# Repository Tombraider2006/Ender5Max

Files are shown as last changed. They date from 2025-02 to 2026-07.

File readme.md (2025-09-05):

<h3 align="right"><a href="https://www.tinkoff.ru/rm/yakovleva.irina203/51ZSr71845" target="_blank">ваше "спасибо" автору</a></h3>
<h3 align="right"><a href="https://t.me/tombraider2006" target="_blank">телеграм канал автора</a></h3>

<h1>ENDER 5 MAX</h1>

Итак вы получили ваш Ender 5 Max.  чтобы не запутаться в мануалах предлагаю маленькую справку по дорожной карте что вам делать дальше.

[**Светлый путь. Дорожная карта что надо сделать с принтером чтобы дальше не мучаться**](/lightway.md)

**Внимание! Ahtung! Attention! все измениения в прошивках вы проводите на свой страх и риск, помните что  после того как вы влезли в програмное или аппаратное обеспечение вы можете потерять гарантию производителя!**

## О прошивке
[**Прошивка и получение root доступа**](/firmware.md)

[**cписок полезных макросов с пояснениями**](/mans/macros.md)

[**Стоковый конфиг**](/stock/)

## Модификации

[**Управляем ретрактом во время печати**](/mans/retract.md) 

[**Установка SFS 2.0**](/mans/sfs2.md) замена стандартного датчика филамента на датчик движения. Предотвратит потерю печати при пробках и петлях в катушках.

[**Установка прошивки Simple Af на Ender 5 Max**](/mans/simpleaf.md) на примере датчика картографер.  

[**Замена хотенда на хотенд от К2**](/mans/k2_hotend.md)

При прошивке SimpleAF понадобится [картографер](https://aliexpress.ru/item/1005006733253744.html?sku_id=12000038123192420)  

[**Прошивка картографера в среде windows с помощью wsl**](/mans/wsl.md)

## О запчастях.

Если необходимо, можно докупить сразу с принтером камеру Nebula . [тут](https://aliexpress.ru/item/1005006159528565.html) или [тут](https://aliexpress.ru/item/1005006124602385.html)

по вопросам приобретения панелей зашивки, а также пластин покрытия стола можно обращаться [@RuLED74](https://t.me/RuLED74)(производство панелей начнется не раньше начала апреля-мая 2025г)

Могу порекомендовать [**магазин на озон**](https://www.ozon.ru/seller/krealiti-3d-427462/?miniapp=seller_427462) и [**магазин в россии**](https://creality-3d.ru/catalog/Ender-5-Max). Не всегда всё есть в наличии но можно и заказать для себя. поставки точно от креалити, а не подделка. В отличии от многих, ребята знают какая запчасть к чему подойдет и могут проконсультировать если надо и проверят. Обычно немного дороже алиэкспресса но надежнее и быстрее. 

## Разное полезное

[**Группа пользователей принтера в телеграм**](https://t.me/Ender_5_Max_Ru)

[**Мини обзор на принтер ENDER 5 MAX**](/review.md)

[**Учебный курс и помощь в прошивке принтера**](/kurs.md)

## ОчУмелые ручки

[**Зачем нам одноплатник?**](/random/pi.md) различные модули которые не могут встать на родную операционную систему однако можно поставить на сторонний сервер **Spoolman**, **Telegram Bot**, **Klipperscreen** написано для к1 серии но с минимальными изменениями применимо и для нашего принтера

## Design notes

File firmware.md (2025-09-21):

<h3 align="right"><a href="https://www.tinkoff.ru/rm/yakovleva.irina203/51ZSr71845" target="_blank">ваше "спасибо" автору</a></h3>
<h3 align="right"><a href="https://t.me/tombraider2006" target="_blank">телеграм канал автора</a></h3>

<h2>Прошивки</h2>

На данный момент получить  `root` можно с помощью прошивки [1.2.0.21](https://www.crealitycloud.com/downloads/firmware/ender-series/ender-5-max) с паролем `creality_2024`

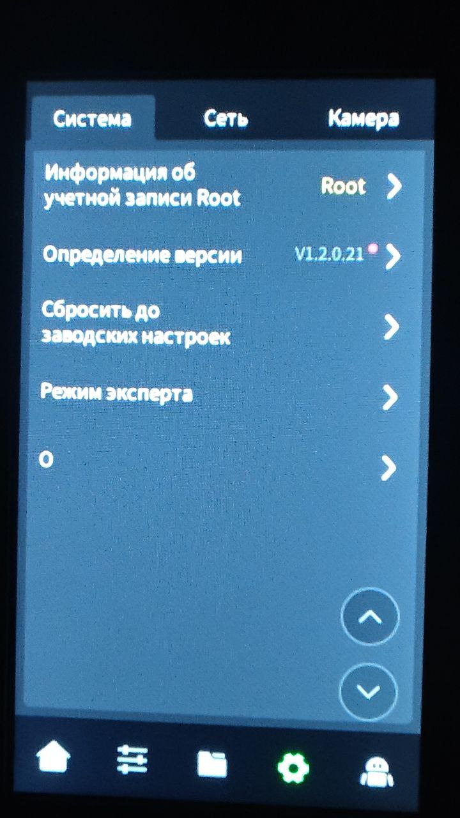
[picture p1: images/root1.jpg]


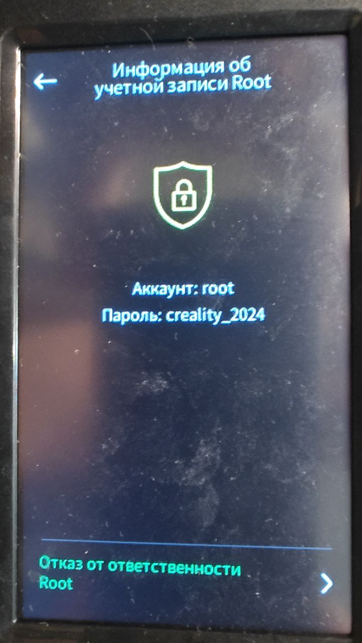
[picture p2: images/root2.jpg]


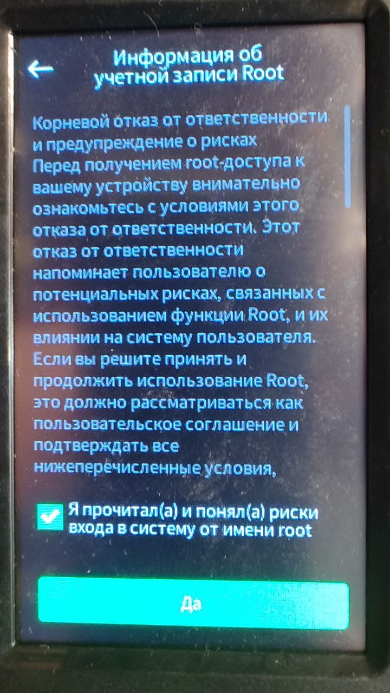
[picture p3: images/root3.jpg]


<details><summary>или с помощью модифицированной прошивки https://github.com/zevaryx/ender-5-max-firmware/releases/latest устарело</summary>

с паролем `creality_2025` 

Если просто залить на флешку установить в принтер и согласиться на обновление не получается и у вас стояла более ранняя прошивка с доступом `root` то можно попробовать заставить обновиться принудительно

```
/etc/ota_bin/local_ota_update.sh /tmp/udisk/sda/*.img
```

или

```
/etc/ota_bin/local_ota_update.sh /tmp/udisk/sda1/*.img
```
после обновления необходимо выключить\включить питание! обязательно!

## Вернуться к прошивке предыдущей 

Чтобы сбросить прошивку, установить более ранюю или вернутся на стоковую прошивку

по ssh заходим и вставляем следующие команды:

```
# Получить текущую версию, независимо от того, какая она
VERSION=$(grep 'ota_version' '/etc/ota_info' | awk -F'=' '{print $2}')

# Принудительно установить версию 1.0.0.0, что ниже минимума
for file in /etc/ota_info /usr/data/creality/userdata/config/system_version.json; do
    sed -i -e "s/${VERSION}/1.0.0.0/g" $file
done

# Перезагрузить систему для принудительной перезагрузки файлов с диска
reboot
```
После этого можно подсунуть системе любую прошивку, она воспримет ее как новую.
</details>
## Установка HELPER-SCRIPT

### Внимание! если вы установите хелпер скрипт то отключите уведомление об обновлении. так же не обновляйте потом прошивку по wifi пока не сбросите принтер до заводских настроек. 

*21.05.2025 -Внимание.*

*Guilois, автор helper script, наконец то обратил внимание на данный принтер и выделил, наконец, ветку под него, но дальнейшего развития не получил, поэтому ставить надо только те пункты которые подойдут нашему принтеру, слепо ставить все подряд нельзя, иначе принтер уйдет в ошибку или перестанет нормально функционировать. 

Пока не приехал ваш картографер, а печатать уже хочется можно облегчить себе жизнь установкой привычной оболочки klipper. Для этого необходимо установить [**хелпер скрипт**](https://guilouz.github.io/Creality-Helper-Script-Wiki/helper-script/helper-script-installation/) и получить базовую функциональность клиппера.

для этого через ssh нам необходимо ввести следующие команды:

```
git clone --depth 1 https://github.com/Guilouz/Creality-Helper-Script.git /usr/data/helper-script
```
после того как скрипт скачается запускаем его

```
sh /usr/data/helper-script/helper.sh
```

пункт 1 install

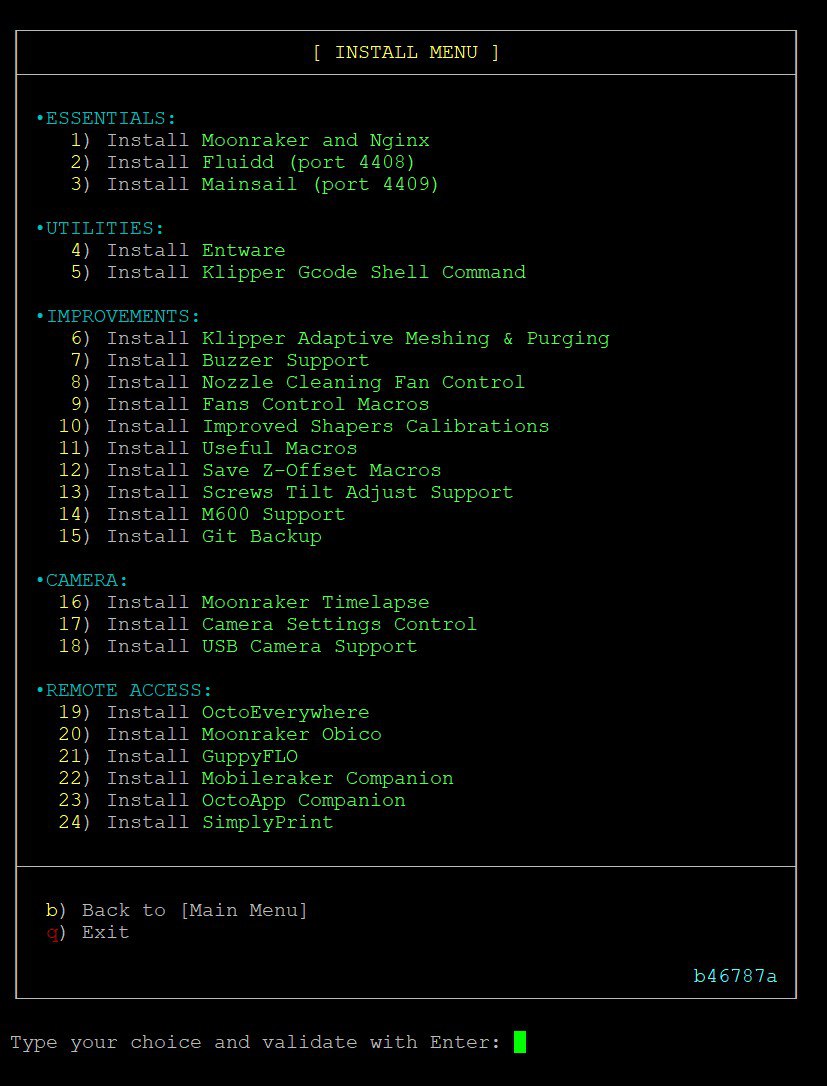
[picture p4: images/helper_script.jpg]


рекомендуемые пункты меню 1, 2, 4, 5, 10. если у вас есть видеокамера то 16.

Лучше сверяйтесь в [**Группе пользователей принтера в телеграм**](https://t.me/Ender_5_Max_Ru) по правильности пунктов. бывает  что могут смениться без предупреждения.

через  браузер теперь мы можем зайти на наш принтер в расширенную вебпанель с доступом к файлам конфигурации и расширенным настройкам. Не забываем указать порт `http://Ваш_ip:4408` если вы установили Fluid и `http://Ваш_ip:4409`  если Mainsail

## После установки

## NEW 
### вариант автоматического внесения изменений

1. Переходим в папку с конфигами принтера. Скачиваем и запускаем скрипт fix_ender5.sh с GitHub

```
wget -q --no-check-certificate https://raw.githubusercontent.com/Tombraider2006/Ender5Max/refs/heads/main/files/fix_e5m.sh -O /tmp/fix_e5m.sh && sh /tmp/fix_e5m.sh
```

<details><summary>Устарело. есть в автоматической версии.</summary>

в вебпанели ищем значок слева {...}  в окошке ищем файл `gcode_macro.cfg` открываем его и мотаем в самый низ

добавим следующий код:

```
[firmware_retraction]
retract_length: 0.45 # безопасное значение для того пластика которым чаще всего печатаете.
retract_speed: 30
unretract_extra_length: 0
unretract_speed: 30

[gcode_shell_command beep]
command: beep
timeout: 2
verbose: False

[gcode_macro BEEP] # звук бип. 
description: Play a sound
gcode:
  RUN_SHELL_COMMAND CMD=beep

[delayed_gcode light_init] 
initial_duration: 5.01
gcode:
  SET_PIN PIN=light_pin VALUE=1

[exclude_object] # исключение обьектов. 

[gcode_macro PID_BED]
gcode:
  PID_CALIBRATE HEATER=heater_bed TARGET={params.BED_TEMP|default(70)}
  SAVE_CONFIG

[gcode_macro PID_HOTEND] # и почему его не было. добавил
description: Start Hotend PID
gcode:
  G90
  G28
  G1 Z10 F600
  M106 S255 #S255 
  PID_CALIBRATE HEATER=extruder TARGET={params.HOTEND_TEMP|default(250)}
  M107

```

сохраняем. 

теперь задачка посложнее. открываем файл `printer.cfg`

ищем параметр `[output_pin Height_module2]` и меняем его на 

```
[output_pin _Height_module2]
```

ищем раздел:

```diff
[output_pin light_pin]
#pin: nozzle_mcu: PB0 #PA10
pin: PC0
value: 0.0
```
меняем на 

```
[output_pin light_pin] #  освещение камеры принтера. косяк прошивки креалити.
pin: !PC0
pwm: True
cycle_time: 0.010
value: 1.0
```

чтобы принтер не шумел обдувом материнской платы при простое. надо заменить раздел

```
[output_pin MainBoardFan]
pin: !PB1
```

меняем на:

```
[controller_fan MCU_fan] # включаем обдув после включения драйверов
pin: PB1
max_power: 1.0
fan_speed: 1
kick_start_time: 0
stepper: stepper_x

```
</details>

Чтобы подготовить принтер к работе пройдем тесты и запишем их в конфиг, сделать это проще чем кажется. Для этого достаточно скопировать код в консоль вебпанели принтера. тесты будут длится около 10-20 минут, после этого принтер перезагрузится и будет готов к работе.

```
PID_BED
PID_HOTEND
INPUT_SHAPER_CALIBRATION
```

## OrcaSlicer
В слайсере орка начиная с 2.3.0 есть готовый профиль под принтер Ender 5 max 

но можно и там найти пару косяков и исправить.

в стартовом коде добавить:

```
M140 S0
M104 S0
```
вот так

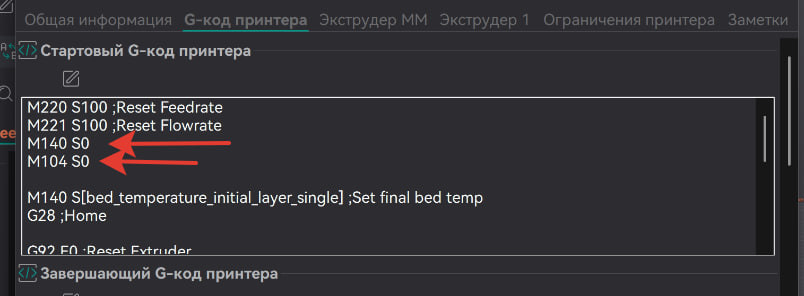
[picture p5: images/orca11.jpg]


**В разделе экструдер** искренно советую понизить скорость ретракта до 30 мм\мсек вместо 50 по умолчанию в 2 местах.

это сохранит шестерни фидера от преждевременного износа.

## Использовать ретракт из прошивки

1. правим стартовый код, добавляем этот блок так:

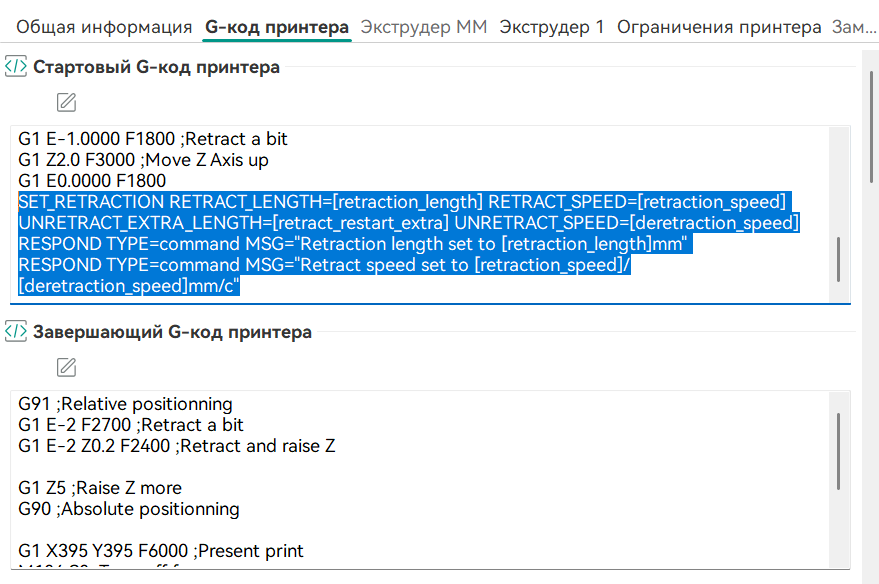
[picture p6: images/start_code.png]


```
SET_RETRACTION RETRACT_LENGTH=[retraction_length] RETRACT_SPEED=[retraction_speed] UNRETRACT_EXTRA_LENGTH=[retract_restart_extra] UNRETRACT_SPEED=[deretraction_speed]
RESPOND TYPE=command MSG="Retraction length set to [retraction_length]mm" 
RESPOND TYPE=command MSG="Retract speed set to [retraction_speed]/[deretraction_speed]mm/c"

```

2. поставим галку тут

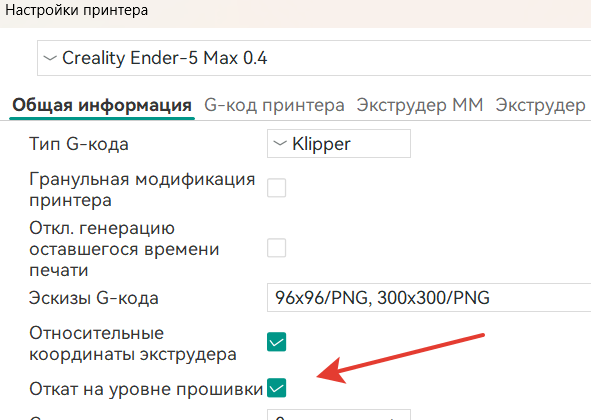
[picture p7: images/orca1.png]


3. потом убираем галку тут

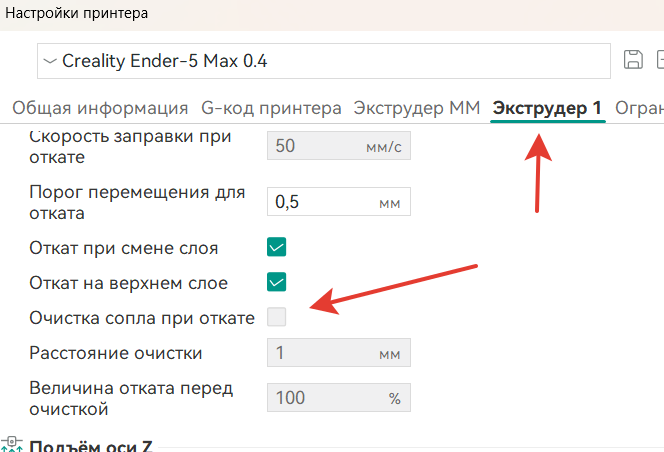
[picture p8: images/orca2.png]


4. не забываем указывать в пластике указывать откат настроенный.

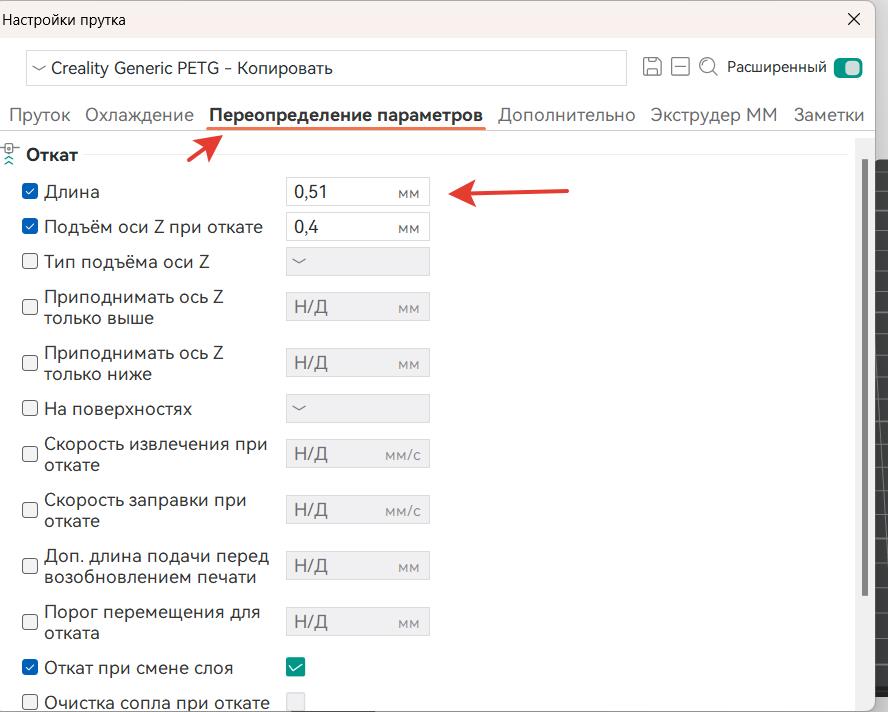
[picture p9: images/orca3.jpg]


## Посмотреть стоковые файлы конфигурации 

1.2.0.10 [тут](/stock/config_1.2.0.10/)

1.2.0.20 [тут](/stock/config_1.2.0.20/)

1.2.0.21 [тут](/stock/config_1.2.0.21/)

На данный момент (август 2025) одна из самых допиленных версий прошивок это от pelkorp с его [**SimpleAF**](https://pellcorp.github.io/creality-wiki/).  К ее недостаткам можно отнести только что поставить можно **!!!только** на картографер и бекон. связано это с тем что не смогли подружить с новым клиппером плату головы а точнее акселерометр. так как в картографере и беконе внутри плат есть акселерометры свои, вышли из положения таким образом.  

Вполне возможно что через некоторое время ситуация измениться.  

Если вы захотите использовать guppyscreen в SimpleAF то необходимо [повернуть экран на 90 градусов.](https://github.com/Tombraider2006/Ender5Max/blob/main/mans/simpleaf.md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) вот [**модель**](/mans/Ender5MaxTiltedScreenMount.stl) чтобы закрепить экран в горизонтальном положении. 

### Если получаем ошибку 2069 (уже есть в автоматическом скрипте)

В файле `printer.cfg` находим разделы и удаляем.

```diff
###喷头前面风扇
[output_pin fan0]
pin: !nozzle_mcu:PB15
pwm: True
cycle_time: 0.01
hardware_pwm: false
value: 0.00
scale: 255
shutdown_value: 0.0
[output_pin en_fan0]
pin: nozzle_mcu: PB6
pwm: False
value: 1.0

###喷头后面风扇
[output_pin fan1]
pin: !nozzle_mcu:PA9
pwm: True
cycle_time: 0.01
hardware_pwm: false
value: 0.00
scale: 255
shutdown_value: 0.0
[output_pin en_fan1]
pin: nozzle_mcu: PB9
pwm: False
value: 1.0

```
заменяем на:

```

[multi_pin part_fans]
pins:!nozzle_mcu:PB15,!nozzle_mcu:PA9

[multi_pin en_part_fans]
pins:nozzle_mcu:PB6,nozzle_mcu:PB9

[fan_generic part]
pin: multi_pin:part_fans
enable_pin: multi_pin:en_part_fans
cycle_time: 0.0100
hardware_pwm: false
```

в файле `gcode_macro.cfg` ищем разделы и удаляем:

```diff
[gcode_macro M106]
gcode:
  {% set fan = 0 %}
  {% set value = 255 %}
  {% if params.S is defined %}
    {% set tmp = params.S|int %}
    {% if tmp <= 255 %}
      {% set value = tmp %}
    {% endif %}
  {% endif %}
  {% if params.P is defined %}
    {% set value = (255 - printer["gcode_macro PRINTER_PARAM"].fan1_min) / 255 * tmp %}
    {% set value = printer["gcode_macro PRINTER_PARAM"].fan1_min + value %}
    {% if value >= 255 %}
      {% set value = 255 %}
    {% endif %}
    SET_PIN PIN=fan1 VALUE={value}

    {% set value = (255 - printer["gcode_macro PRINTER_PARAM"].fan0_min) / 255 * tmp %}
    {% set value = printer["gcode_macro PRINTER_PARAM"].fan0_min + value %}
    {% if value >= 255 %}
      {% set value = 255 %}
    {% endif %}
    SET_PIN PIN=fan0 VALUE={value}
  {% else %}
    {% set value = (255 - printer["gcode_macro PRINTER_PARAM"].fan1_min) / 255 * tmp %}
    {% set value = printer["gcode_macro PRINTER_PARAM"].fan1_min + value %}
    {% if value >= 255 %}
      {% set value = 255 %}
    {% endif %}
    SET_PIN PIN=fan1 VALUE={value}

    {% set value = (255 - printer["gcode_macro PRINTER_PARAM"].fan0_min) / 255 * tmp %}
    {% set value = printer["gcode_macro PRINTER_PARAM"].fan0_min + value %}
    {% if value >= 255 %}
      {% set value = 255 %}
    {% endif %}
    SET_PIN PIN=fan0 VALUE={value}

  {% endif %}
  {% if tmp < 1 %}
    {% set value = tmp %}
    SET_PIN PIN=fan0 VALUE={value}
    SET_PIN PIN=fan1 VALUE={value}
  {% endif %}

[gcode_macro M107]
gcode:
  {% if params.P is defined %}
    SET_PIN PIN=fan0 VALUE=0
    SET_PIN PIN=fan1 VALUE=0
  {% else %}
    SET_PIN PIN=fan0 VALUE=0
    SET_PIN PIN=fan1 VALUE=0
  {% endif %}

```
заменяем на:

```
[gcode_macro M106]
description: Set Fan Speed. P0 for part
gcode:
  {% set fan_id = params.P|default(0)|int %}
  {% if fan_id == 0 %}
    {% set speed_param = params.S|default(255)|int %}
    {% if speed_param > 0 %}
      {% set speed = (speed_param|float / 255) %}
    {% else %}
      {% set speed = 0 %}
    {% endif %}
    SET_FAN_SPEED FAN=part SPEED={speed}
  {% endif %}

[gcode_macro M107]
description: Set Fan Off. P0 for part
gcode:
  SET_FAN_SPEED FAN=part SPEED=0

[gcode_macro TURN_OFF_FANS]
description: Stop chamber, auxiliary and part fan
gcode:
    SET_FAN_SPEED FAN=part SPEED=0

[gcode_macro TURN_ON_FANS]
description: Turn on chamber, auxiliary and part fan
gcode:
    SET_FAN_SPEED FAN=part SPEED=1

```
в самом верху файла ищем  и удаляем строки

```
variable_fan0_min: 90 #240 #90
variable_fan1_min: 70 #240 #70
```

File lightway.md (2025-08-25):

# Светлый путь

1. собираем принтер. проверяем комплектацию. Запускаем принтер проходим начальную калибровку.  если возникают ошибки не переживаем ищем ответы в чате.
2. прошиваем принтер на [**прошивку в которой есть доступ root**](/firmware.md). Без этого принтер практически калека.
3. Заказываем [картографер](/mans/simpleaf.md), [sfs 2.0](/mans/sfs2.md)  на алиэкспресс. Ждем зеленея от надежды. Ищем в мануалах файлы моделей необходимых для установки, не торопясь распечатываем. Возможно не спервого раза. 
4. Пока ждем модели снимаем карту стола.  видим большой горб в 1-2мм на стол, не расстраиваемся идем в чат узнаем что нам надо купить мягкое железо, кусок стекла 415х415мм и еще одно магнитное основание.
5. Регулируем ремни. Мануал будет позже. пока можно посмотреть видео на ютубе от креалити. модели упоров скачать [тут левый](/files/X-axis+tensioning+tool-20250220.stl) [тут правый](/files/Y-axis+tensioning+tool-20250220.stl)
6. Получаем детали, устанавливаем, [датчик движения филамента sfs 2.0](/mans/sfs2.md).
7. Прошиваем картографер [**так**](https://pellcorp.github.io/creality-wiki/cartographer_flashing/#flashing-k1-firmware-via-dfu-mode) или [**так**](/mans/dfu.md)
8. Устанавливаем картографер на принтер. Модели для печати смотрим в пункте 9. Вспоминаем, что забыли купить стяжки чтобы прикрепить провод, плюемся, идем в ближайший магазин покупаем, крепим.
9. Устанавливаем [**прошивку SimpleAF**](/mans/simpleaf.md) 
10. Наши мучения окончены, забываем про софт креалити. Никакие обновления от них в будущем вам не нужны!

## Наши руки не для скуки.

1. Если вам не хватило развлечений, то пишем в [**магазин на озон**](https://www.ozon.ru/seller/krealiti-3d-427462/?miniapp=seller_427462) и [**магазин в россии**](https://creality-3d.ru/catalog/Ender-5-Max) что хотим себе зашивку на принтер. Это даст возможность не только круто выглядеть но и печатать принтеру высокотемпературными пластиками такими как АБС. 
2. Очень предусмотрительно с Вашей стороны будет заказать шестерни экструдера к1с. Да-да, фидер на принтере именно от него. так что смело заказываем. 

3. Сопла для принтера - расходник. Так что заказываем тоже. Ссылка на магазин выше.
4. Возможно вас заинтересует возможность [**смены хотенда на хотенд от К2**](/mans/k2_hotend.md).
5. [**кастомные петли для передней дверцы зашивки**](/files/door190.zip), в отличии от штатных у которых 100 градусов открытие на 190  градусов

BOM
Ось **М3х30**, под нее просто нарезать резьбу, крепление **М3х14**, в **вплавляемые гайки**.

Счастливого светлого пути в мир 3д печати!

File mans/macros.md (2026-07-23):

<h3 align="right"><a href="https://www.tinkoff.ru/rm/yakovleva.irina203/51ZSr71845" target="_blank">ваше "спасибо" автору</a></h3>
<h3 align="right"><a href="https://t.me/tombraider2006" target="_blank">телеграм канал автора</a></h3>
<h5 align="right">поставьте "звездочку" проекту. так другим пользователям легче его найти.</h5>

## cписок полезных макросов с пояснениями

После установки хелпер скрипта открывая вашу панель вы можете увидеть огромную "простыню" с всевозможными макросами. В основном они системные и не предполагают никакого взаимодействия с вами. Они от системы для системы и про систему. Чтобы не путаться и не захламлять интерфейс можно провести несколько простых операций:

1 - открываем настройки

2 - нажимаем макросы

3 - добавить категорию

4 - вписываем название категории (у меня это "тесты")

5 - жмем сохранить

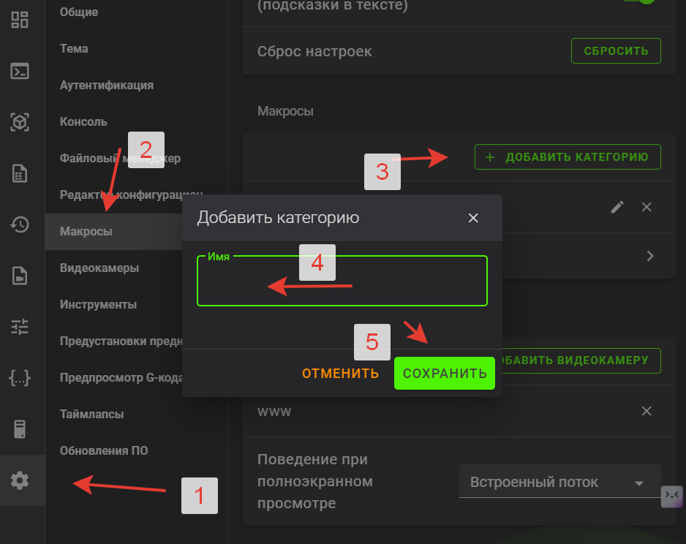
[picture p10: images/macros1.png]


Теперь переходим в раздел "вне категории" и по следующему списку выбираем макрос и нажимаем на него и выбираем ему нашу свежесозданную категорию

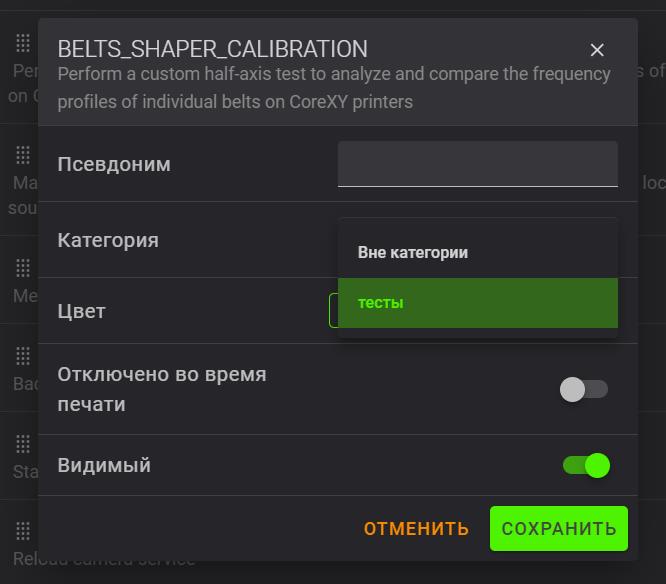
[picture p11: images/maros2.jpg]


`BELTS_SHAPER_CALIBRATION` делает тест резонансов и создает график натяжения ремней

`EXCITATE_AXIS_AT_FREQ` макрос тестирования на определенной частоте резонансов для выявления дефектов сборки

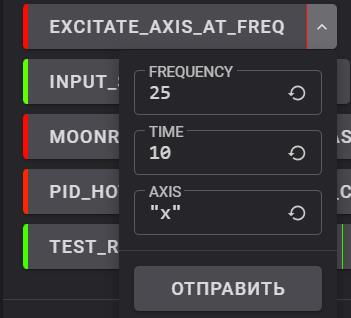
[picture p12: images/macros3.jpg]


На картинке выше мы видим значения по умолчанию. на частоте 25 герц в течении 10 секунд трясем осью икс.  для проведения теста мы ставим 3-5 секунд и перебором частот 25, 27, 30.. и т.д. находим частоту на которой вибрации максимальны. Далее ставим время теста 30-40 секунд и пальпируя корпус находим узел который  вызывает резонанс.  Внешним осмотром выявляем проблему(выкрутился болтик, отклеилась панель, недотянут винт и прочее)  

`INPUT_SHAPER_CALIBRATION` делает тест резонансов и записывает результат в `printer.cfg`

В стоковой прошивке выбор шейперов ограничен `ei` что далеко не оптимально. Helper script решает эту проблему, поэтому после установки скрипта необходимо использовать этот  макрос для установки правильных шейперов.

`TEST_RESONANCES_GRAPHS` делает тест резонансов и записывает его в график.

На основании графика легче понять какие есть проблемы в кинематике, выбрать максимальные ускорения в слайсере, проверить насколько правильно автокалибратор поставил значения в `printer.cfg` 

После окончания теста в папке: `/Helper-Script/improved-shapers` будут находится наши графики. 

В случае прошивки Simple AF графики будут в папке `/images`

`PID_BED` это процедура калибровки, которая гарантирует, что принтер всегда будет поддерживать стабильную заданную температуру . PID (пропорционально-интегральная производная) используется в принтерах для поддержания стабильной температуры стола. По умолчанию тест идет на 70 градусах но рядом со значком есть стрелка вниз раскрываем и устанавливаем там температуру на которой мы в основном работаем.

`PID_HOTEND` это процедура калибровки, которая гарантирует, что принтер всегда будет поддерживать стабильную заданную температуру . PID (пропорционально-интегральная производная) используется в принтерах для поддержания стабильной температуры в хотенде. По умолчанию тест идет на 250 градусах но рядом со значком есть стрелка вниз раскрываем и устанавливаем там температуру на которой мы в основном работаем.

`TILT_TABLE` автоматическая регулировка наклона стола. 

**ТОЛЬКО** для прошивки Simple Af Ender 5 Max

Алгоритм:

1. домой по всем осям
2. быстро вниз на 400 (это не до упора)
3. "обман" высоты, как будто Z не 400, а 370 
4. медленно вниз = долгожданный треск ****
5. ещё раз "обман" (контрольный)
6. ещё медленнее и ещё немного потрещим ***
7. быстро вверх почти домой, но нет...
8. дом Z (стандартно домой Z)

Макрос копируем в любое место в printer.cfg
Сохраняем с перезапуском клипера.
Далее в разделе "макросы" видим новый пункт "tilt_table". 
При желании в настройках макросов можно переименовать эту кнопку в привычный язык "наклон" и задать любой цвет (маркер) кнопки. 
Если кого напрягает скорость стола, можете уменьшить или увеличить значение (F1300). 

```
[gcode_macro tilt_table]
gcode:
    G28
    G0 Z400 F1300
    SET_KINEMATIC_POSITION Z=370 
    {% set driver_config = printer.configfile.settings['tmc2209 stepper_z'] %}
    {% set RUN_CUR = driver_config.run_current|float %}
    {% set HOME_CUR = 0.45 %}
    SET_TMC_CURRENT STEPPER=stepper_z CURRENT={HOME_CUR}
    G0 Z400 F600
    SET_KINEMATIC_POSITION Z=390
    G0 Z400 F300
    SET_TMC_CURRENT STEPPER=stepper_z CURRENT={RUN_CUR}
    G0 Z20 F1300
    G28 Z
```

После этого ваша вебпанель приобретет более аккуратный вид и нужные вам макросы будут более наглядно расположены. 

Для прошивки Simple AF все вышесказанное также справедливо, однако чуть другие названия макросов.

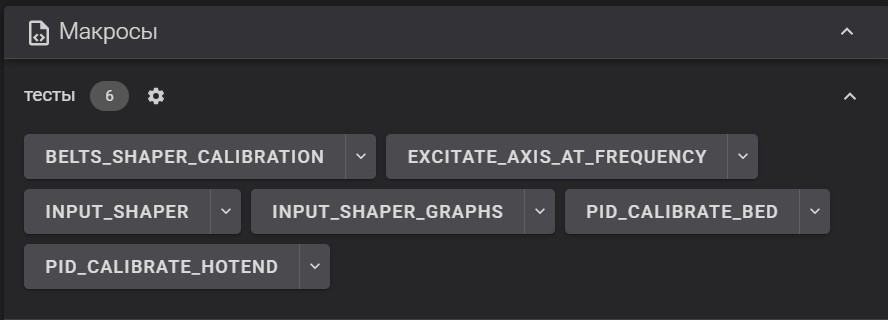
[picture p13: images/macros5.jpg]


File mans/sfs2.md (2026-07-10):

<h3 align="right"><a href="https://www.tinkoff.ru/rm/yakovleva.irina203/51ZSr71845" target="_blank">ваше "спасибо" автору</a></h3>
<h3 align="right"><a href="https://t.me/tombraider2006" target="_blank">телеграм канал автора</a></h3>
<h5 align="right">поставьте "звездочку" проекту. так другим пользователям легче его найти.</h5>

## Установка датчика движения филамента вместо стандартного датчика окончания филамента

[**english version**](/mans/sfs2_en.md)

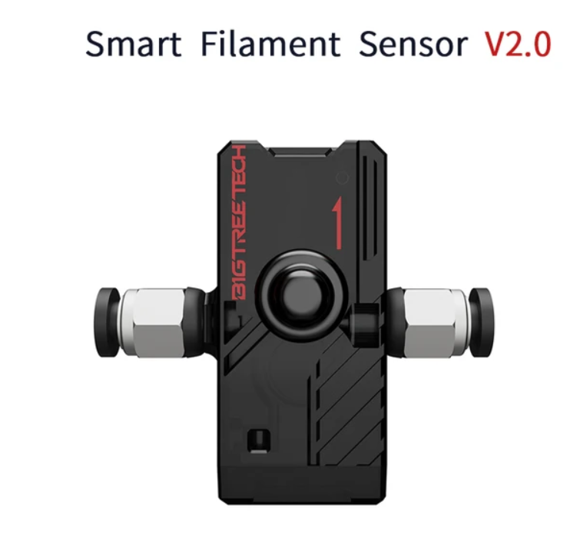
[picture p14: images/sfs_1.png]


Учитывая большую область печати на этом принтере, значительное время печати и высокий расход филамента, контроля только за его окончанием явно недостаточно. Цена ошибки в случае застревания материала будет крайне высока, поэтому установка системы мониторинга не только окончания, но и застревания филамента — отличное решение.

Это позволит минимизировать риски сбоев и избежать потерь времени и материалов.

Так как в обычном датчике филамента у нас три провода, а в sfs 2.0 их 4 то есть два способа установки. 
* первый предполагает соединение только датчика движения вместо окончания филамента, что логично. если нет филамента то он и не движется, что все равно приведет к сработке.
* однако в конструкции нашего принтера не так уж и сложно подвести дополнительный провод, так что этот вариант мы тоже рассмотрим. 

## Первый способ

(замена датчика без дополнительной проводки)

Для этого нам нужно переставить провода в колодку на 4 провода. например так:

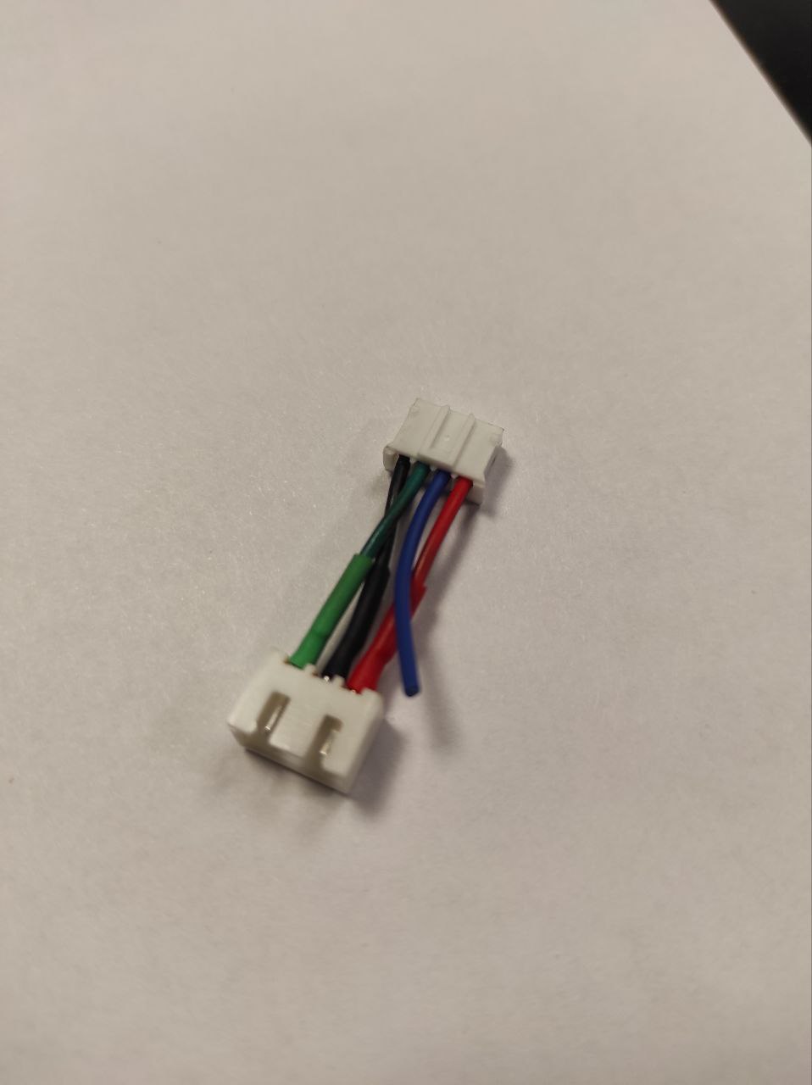
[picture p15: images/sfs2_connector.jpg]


значения на коннекторе следующие:

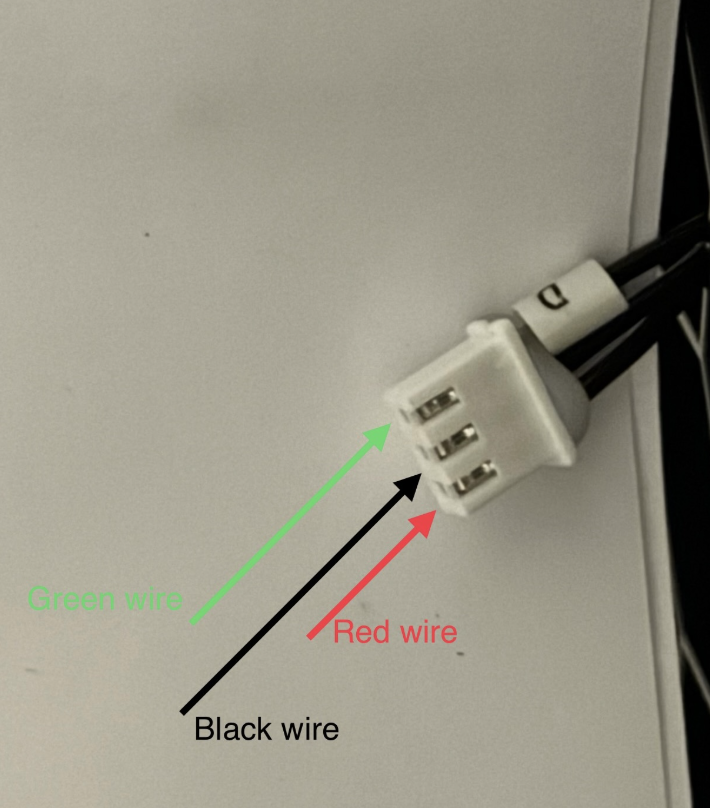
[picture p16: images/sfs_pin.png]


Далее заходим в `printer.cfg` и ищем строки:

```
[filament_switch_sensor filament_sensor] # датчик филамента
switch_pin: !PC6
pause_on_runout: true
```

и заменяем на:

```
[filament_motion_sensor filament_sensor]
detection_length: 5.3
extruder:extruder
pause_on_runout: true
switch_pin: ^PC6
runout_gcode:
  RESPOND TYPE=command MSG="Filament runout/blocked!"
insert_gcode:
  RESPOND TYPE=command MSG="Filament inserted"

```

**или** можем побаловаться с оповещением и при паузе прозвучит несколько звуковых сигналов

```
[gcode_shell_command beep]
command: beep
timeout: 2
verbose: False

[gcode_macro BEEP]
description: Play a sound
gcode:
  RUN_SHELL_COMMAND CMD=beep

[filament_motion_sensor encoder_sensor]
switch_pin: ^!PC6
detection_length: 5.3 # возможно сделать чуть меньше 2.7 по умолчанию
extruder: extruder
runout_gcode:
  _ON_FILAMENT_RUNOUT # для симпл аф!!!!
  RESPOND TYPE=command MSG="Filament runout/blocked!"
  UPDATE_DELAYED_GCODE ID=sfs_alarm DURATION=1
insert_gcode:
  RESPOND TYPE=command MSG="Filament inserted"
  UPDATE_DELAYED_GCODE ID=sfs_alarm DURATION=0

[delayed_gcode sfs_alarm]
# initial_duration: 0
gcode:
  beep
  beep
  beep
  beep
  beep
  beep
  #UPDATE_DELAYED_GCODE ID=sfs_alarm DURATION=1 #если убать комент в начале строки то сигналы будут постоянно.
```
## Второй способ

Если ваши руки не для скуки то можно получить полную функциональность датчика с меньшим количеством отказов для этого надо задействовать все 4 провода от датчика. 

*По сути внутри корпуса sfs находится 2 датчика, датчики наличия филамента, и датчик движения филамента. Для этого нам и нужен четвертый провод.*

Для начала, я соеденил конектор из комплекта через переходник(*дендрофекальным способом*)

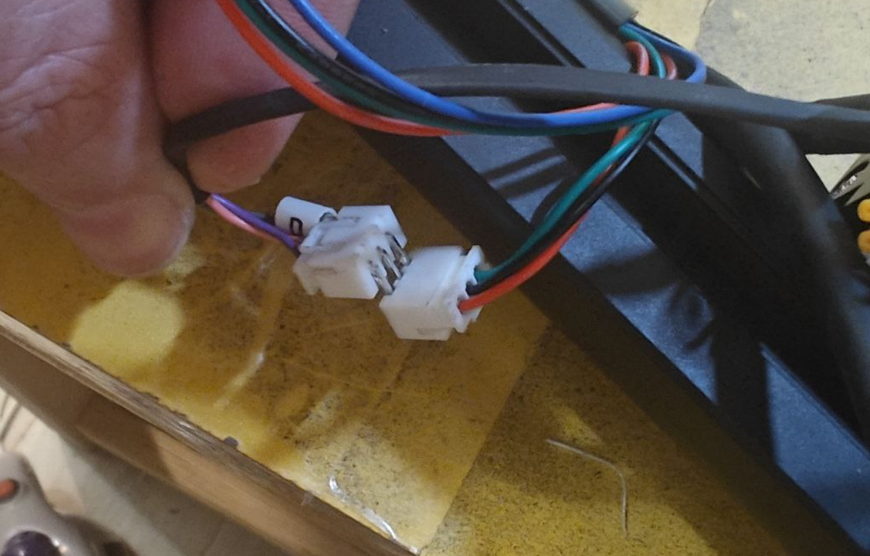
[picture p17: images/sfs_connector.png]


Оставшийся **синий** провод надо протянуть до нашей материнской платы и и припаять к этому выходу. На фото он красный потому что родного провода не хватает буквально 10 сантиметров и я его нарастил. 

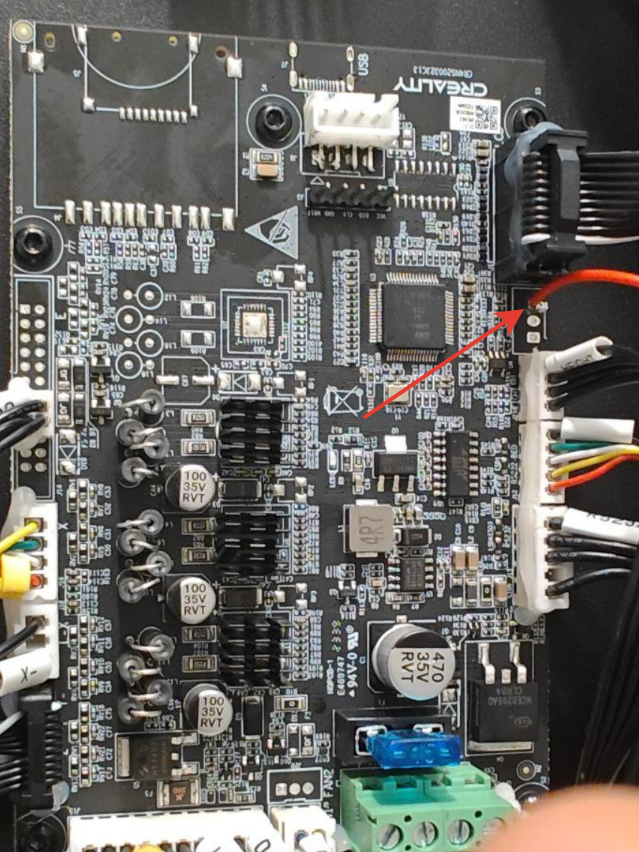
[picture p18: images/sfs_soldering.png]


заходим в `printer.cfg` и ищем строки:

```
[filament_switch_sensor filament_sensor] # датчик филамента
switch_pin: !PC6
pause_on_runout: true
```

и заменяем на:

```
[gcode_shell_command beep]
command: beep
timeout: 2
verbose: False

[gcode_macro BEEP]
description: Play a sound
gcode:
  RUN_SHELL_COMMAND CMD=beep

[filament_switch_sensor filament_sensor]
switch_pin: PA15
pause_on_runout: true
# runout_gcode: PAUSE

[filament_motion_sensor encoder_sensor]
switch_pin: ^!PC6
detection_length: 5.3
extruder: extruder
runout_gcode:
  _ON_FILAMENT_RUNOUT # для симпл аф!!!!
  RESPOND TYPE=command MSG="Filament runout/blocked!"
  UPDATE_DELAYED_GCODE ID=sfs_alarm DURATION=1
insert_gcode:
  RESPOND TYPE=command MSG="Filament inserted"
  UPDATE_DELAYED_GCODE ID=sfs_alarm DURATION=0

[delayed_gcode sfs_alarm]
# initial_duration: 0
gcode:
  beep
  beep
  beep
  beep
  beep
  beep
```
### Установка

Для установки необходимо заменить платформу датчика филамента. модель скачиваем [**отсюда**](/files/Ender5MaxSFSMount.stl) 

Выглядит это так

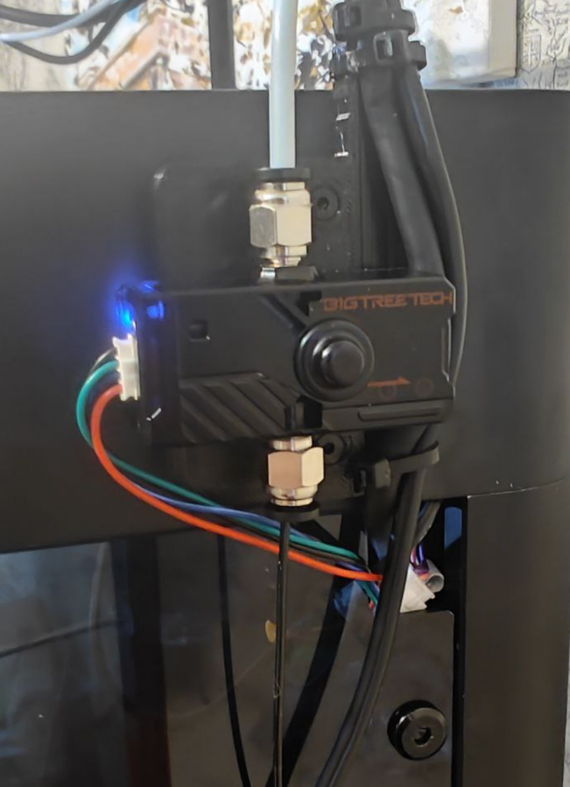
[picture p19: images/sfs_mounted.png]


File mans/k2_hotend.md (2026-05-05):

# Замена хотенда на хотенд от к2

На данный момент с хотендом от Ender 5 Max существует несколько проблем.
1. Нет в продаже самого хотенда. update(уже есть)
2. Нет сопел под него кроме размера 0.4 update(иногда найти тяжело. но уже бывают)
3. Из-за оcобенностей конструкции частые протечки сверху хотенда со стороны горла.
4. На соплах от К2 почти всегда есть носик из закаленной стали что позволит нам печатать композитами.

Чтобы обойти эти проблемы было решено купить хотенд от принтера Creality K2.

### Какие проблемы нас ждут при переходе.

1. Радиаторы хотендов несовместимы. поэтому придется оставлять радиатор от Ender 5 Max(E5M в дальнейшем).
2. Длина проводов у К2 меньше чем у E5M.
3. Длина носика сопла чуть меньше, что не критично но отметить надо.

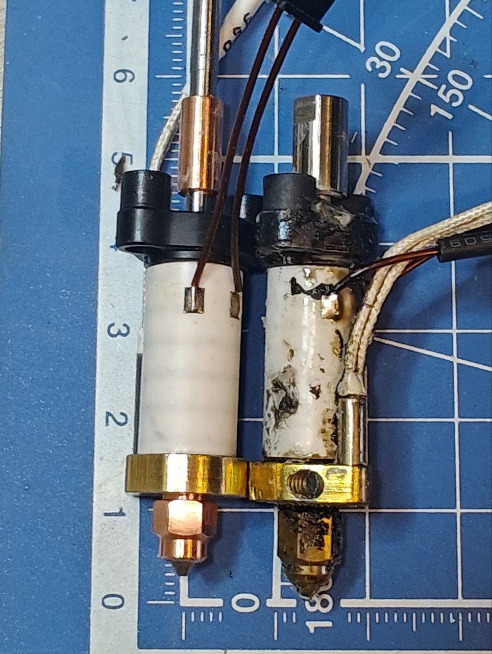
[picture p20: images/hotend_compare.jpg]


4. Диаметр горла Е5М 6mm диаметр медной насадки на сопле unicorn 4.75mm

### Материалы и инструменты. 

1. Медная трубка 6мм диаметром с толщиной стенки 0.5 и длиной 10мм. Купить можно [**тут**](https://prodiel.ru/trubka-mednaya-m2t-6-kh-05-mm-1-metr) или [тут](https://ozon.ru/t/OLvbYkH)
2. набор шестигранников комплекта Е5М
3. термоусадка.
4. Хотенд от к2 в сборе. магазин наших друзей [**тут**](https://creality-3d.ru/catalog/Ender-5-Max)
5. Термопаста. Перфекционисты могут смазать как трубку так и радиатор сопла.

### Порядок замены.
1. снимаем хотенд в сборе. Для этого достаточно открутить 2 винта, отсоединяем разьемы нагревателя, термистора, вентилятора. Вентилятор откручиваем от хотенда. 

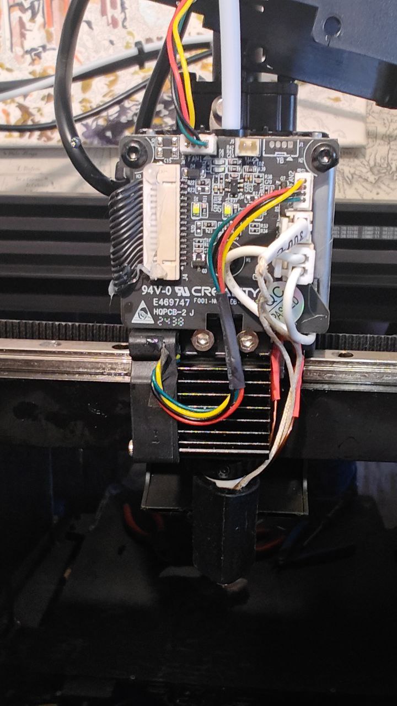
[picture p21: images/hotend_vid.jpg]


2. На снятом хотенде откручиваем сам хотенд от радиатора, не забываем ослабивть винт взади который прижимает горло.

3. В радиатор вставляем кусок медной трубки длиной 10мм.

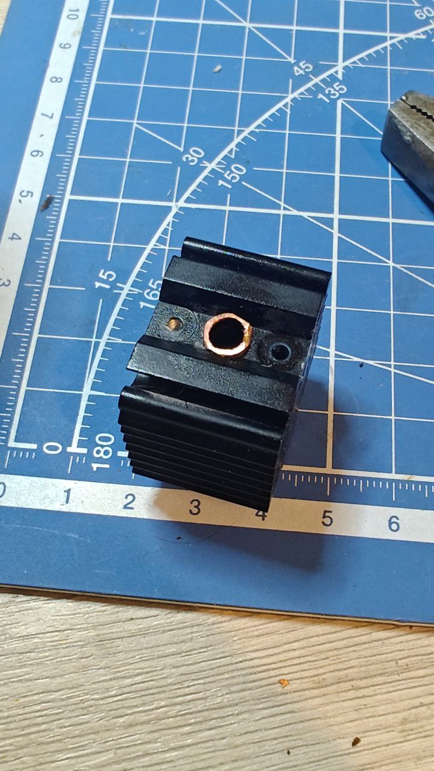
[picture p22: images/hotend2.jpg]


4. Я для ускорения работ ослабил крепеж термистора на обоих хотендах и заменил на хотенде к2 термистор от Е5М. так проводов хватит без необходимости их удлинять.

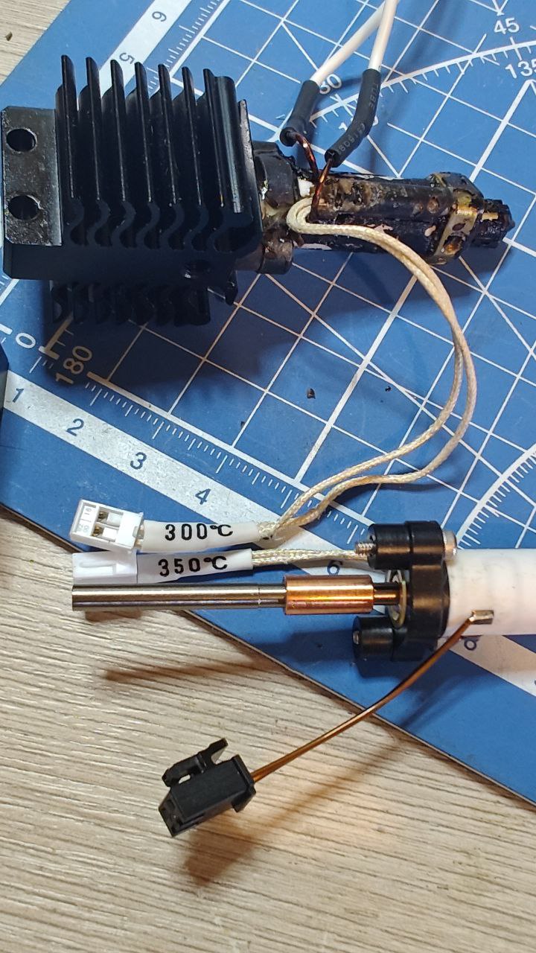
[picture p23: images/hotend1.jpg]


5. разрезаем провода нагревателя и соединяем их с проводами нагревателя от к2

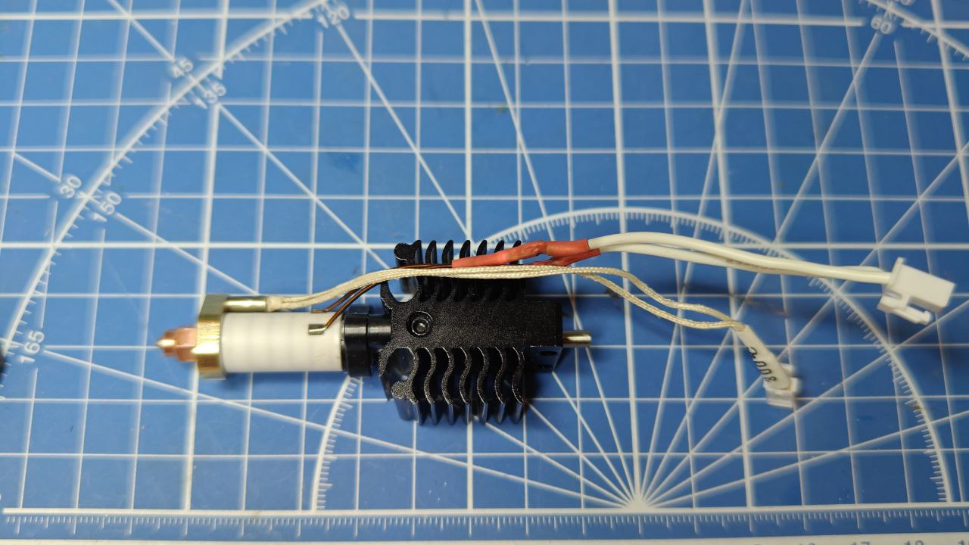
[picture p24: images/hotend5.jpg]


6. Собираем все вместе. устанавливаем обратно.

7.  после включения можно дать команду на калибровку хотенда с новым соплом. например так:

```
PID_CALIBRATE HEATER=extruder TARGET=250
```

### P.S. 

Если у вас установлена прошивка Simple AF то необходимо отклалибровать ваш датчик вихревых токов заново. [модель передней крышки с измененными расстоянимя от стола до датчика](/files/front_cover_carto.stl). Так как сопло короче, возникает ошибка изза недостаточной высоты от стола.

### P.P.S

Информация для перфекционистов. 

Если вы решили оставить термистор от Хотенда К2 и хотите правильно вписать тип термистора то вам необходимо следующее:

Открыть файл `printer.cfg`

Перед разделом `[extruder]` вставляем секцию:

```
[thermistor my_thermistor]
temperature1:25
resistance1:260000
temperature2:220
resistance2:738
temperature3:350
resistance3:98
```
в разделе `[extruder]` ищем параметр `sensor_type` и меняем эту строку на:

```
sensor_type: my_thermistor
```

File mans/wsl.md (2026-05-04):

## Прошивка картографера с помощью Wsl из Windows

### Установка wsl

Открываем командную строку windows пишем `cmd` в поиске правой кнопкой мыши на иконке и ищем строку **запуск с правами администратора**

```
wsl --install
```
*Примечание:
Приведенная выше команда работает только в том случае, если WSL не установлен вообще. Если вы запускаете `wsl --install` и видите текст справки WSL, попробуйте `wsl --list --online` просмотреть список доступных дистрибутивов и запустить `wsl --install -d <DistroName>` для установки дистрибутива.*

Подробно про  установку можно [почитать тут](https://learn.microsoft.com/ru-ru/windows/wsl/install) 

**После установки обязательно перезагрузить компьютер!**
иначе будет у вас ошибка вылезать.

### Устанавливаем ubuntu 
вполне возможно что при установке wsl у вас и так установилась ubuntu. но чтобы быть уверенными поставим более правильный пакет.
```
wsl.exe --install Ubuntu-24.04
```



после установки вероятнее всего запустится автоматически и предложит ввести имя и потом пароль дважды. если не запустилось : 

#### Запуск Ubuntu
```
wsl.exe -d Ubuntu-24.04
```

 вписываем имя пользователя и пароль, пароль отображаться не будет, это нормально, повторяем ввод пароля

будет правильным сразу проверить и установить обновления

```
sudo apt update && sudo apt upgrade -y
```

выходим пока из установленного дистрибутива, так как нам надо еще доустановить пакет для usb подключения.  

```
exit
```
### Увидеть USB в Linux 

Устанавливаем пакет для того чтобы видеть подключенные usb устройства 

```
winget install --interactive --exact dorssel.usbipd-win
```

Список всех USB-устройств, подключенных к Windows, откройте PowerShell **в режиме администратора** и введите следующую команду. После перечисления устройств выберите и скопируйте идентификатор шины устройства, который вы хотите подключить к WSL.
```
usbipd list
```



**Обратите внимание на номер BUSID у себя, он может отличаться от того что в мануале**

Перед присоединением USB-устройства необходимо использовать команду usbipd bind для совместного использования устройства, что позволяет подключить его к WSL. Для этого требуются права администратора. Выберите идентификатор шины устройства, который вы хотите использовать в WSL, и выполните следующую команду. После выполнения команды убедитесь, что устройство используется совместно, повторно выполнив команду `usbipd list`.

```
usbipd bind --busid 1-2
```



1. Чтобы подключить USB-устройство, выполните следующую команду. (Вам больше не нужно использовать командную строку администратора с повышенными привилегиями.) Убедитесь, что командная строка WSL открыта, чтобы поддерживать работу  виртуальной машины WSL 
2. Обратите внимание, что до тех пор, пока USB-устройство подключено к WSL, оно не может использоваться Windows. После подключения к WSL USB-устройство может использоваться любым дистрибутивом, работающим как WSL 
3. Убедитесь, что устройство подключено с помощью `usbipd list`. В командной строке WSL выполните команду lsusb , чтобы убедиться, что USB-устройство отображается и может взаимодействовать с помощью средств Linux.

*Если например при выводе*:

```
BUSID  VID:PID    DEVICE
1-2    1d50:614e  Cartographer
```
то вписываем 1-2 в команде. **Внимание номер должен быть ваш а не из примера!**

```
usbipd attach --wsl --busid 1-2 --auto-attach
```

*не забываем заменить `<busid>` на свое значение*



Если появилась надпись красным. 



Не переживаем и в соседнем окне просто включаем наш линукс.
```
wsl.exe -d Ubuntu-24.04
```
и повторяем попытку запуска в предыдущем окне

```
usbipd attach --wsl --busid <ваш номер> --auto-attach
```

*не забываем заменить `<ваш номер>` на свое значение*

Важно! мы специально добавили `--auto-attach` он пригодится нам в дальнейшем при запуске скрипта.

### Откройте Ubuntu 

```
wsl.exe -d Ubuntu-24.04
```

установим утилиты usb 

```
sudo apt install usbutils
```
затем проверим наконец что же у нас на портах usb

```
lsusb
```



Вы увидите только что подключенное устройство и сможете взаимодействовать с ним с помощью обычных средств Linux. 

подробно можно [почитать тут](https://learn.microsoft.com/ru-ru/windows/wsl/connect-usb)

### Прошивка картографера

Вам необходимо выполнить следующие команды для установки необходимых пакетов.

```
sudo apt-get install virtualenv python3-dev python3-pip python3-setuptools libffi-dev build-essential git dfu-util
```

ПО для картографера

```
git clone "https://github.com/Klipper3d/klipper" $HOME/klipper
git clone "https://github.com/Cartographer3D/cartographer-klipper.git" $HOME/cartographer-klipper
```
чтобы прошить прошивку 5.1.0, вам нужно скачать последнюю версию master и переключиться на нее. Это можно сделать следующим образом:

```
cd $HOME/cartographer-klipper
git fetch
git switch master
git reset --hard origin/master
```
Настройка виртуального окружения Klipper

```
virtualenv --system-site-packages $HOME/klippy-env
$HOME/klippy-env/bin/pip3 install -r $HOME/klipper/scripts/klippy-requirements.txt
```

**проверяем что все сделано правильно:**

```
lsusb
```
должен появится вывод что то типа `1d50:614e` в списке id

### Прошивка 

```
CARTO_DEV=$(ls /dev/serial/by-id/usb-* | grep -E "IDM|Cartographer" | head -1) && cd $HOME/klipper/scripts && sudo -E $HOME/klippy-env/bin/python -c "import flash_usb as u; u.enter_bootloader('$CARTO_DEV')" && echo "⏳ Ждём переподключение устройства..." && sleep 3 && for i in {1..20}; do KATAPULT_DEV=$(ls /dev/serial/by-id/usb-katapult* 2>/dev/null) && [ -n "$KATAPULT_DEV" ] && break; sleep 0.5; done && sudo -E $HOME/klippy-env/bin/python $HOME/klipper/lib/katapult/flashtool.py -f $HOME/cartographer-klipper/firmware/v2-v3/survey/5.1.0/Survey_Cartographer_K1_USB_8kib_offset.bin -d $KATAPULT_DEV
```

**Что в данной команде.**

Устройство работает как usb-Cartographer

Скрипт делает enter_bootloader

Устройство переподключается как usb-katapult

Windows автоматически делает attach в WSL

Скрипт ловит новый /dev/serial/by-id

Прошивка через Katapult

Вы должны увидеть примерно такой вывод:

```
Connecting to Serial Device /dev/serial/by-id/usb-katapult_stm32f042x6_2F003D001653584833373720-if00, baud 250000
Detected USB device running Katapult
Attempting to connect to bootloader
Katapult Connected
Software Version: ?
Protocol Version: 1.0.0
Block Size: 64 bytes
Application Start: 0x8002000
MCU type: stm32f042x6
Flashing '/home/ujif8/cartographer-klipper/firmware/v2-v3/survey/5.1.0/Survey_Cartographer_K1_USB_8kib_offset.bin'...

[##################################################]

Write complete: 22 pages
Verifying (block count = 351)...

[##################################################]

Verification Complete: SHA = E0F7104BECCF44EDBB9346C237C28A42AF072BEC
Programming Complete

```



Подробнее можно [прочитать тут](https://pellcorp.github.io/creality-wiki/cartographer_V3_flashing/)

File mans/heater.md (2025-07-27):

# Активная термокамера для Ender 5 Max

После установки штатной зашивки возникает желание попечатать пластики с высокой усадкой(ABS, PA и прочие)

Второй момент это печать обычных пластиков, большую крышку снимать и укладывать достаточно проблематично особенно при дефиците места.

Все эти проблемы мы постараемся решить с помощью создания дополнительного оборудования. 

1. Нагреватель камеры. призван ускорить и стабилизировать температуру внутри принтера

2. Дополнительные вентиляторы обдува должны обеспечить отток горячего воздуха, если это необходимо. Особенно это важно при печати легкоплавкими пластиками типа PLA, PETG и подобных

Так как материнская плата принтера бедна на разьемы и пины, необходимо добавить дополнительную плату mcu которая обеспечит весь этот праздник жизни.

## Материалы и инструменты.

1. Дополннительная плата mcu - [expander mcu Voron](https://aliexpress.ru/item/1005002394568889.html)
2. [Gdstime GDB 12032 Пластиковый вентилятор 12см 24В](https://aliexpress.ru/item/1005002311794444.html)
3. [Вентилятор охлаждения, кулер DC12025HBL 24V, 120на120на25мм, подшипник качения **2 штуки**](https://www.ozon.ru/product/ventilyator-ohlazhdeniya-kuler-dc12025hbl-24v-120-120-25mm-podshipnik-kacheniya-1990050205/)
4. [Автоматический выключатель 10А SSR-10DA](https://www.ozon.ru/product/avtomaticheskiy-vyklyuchatel-10a-1661490786/)
5. [PTC Нагреватель Керамический Постоянной Температуры Высокого Напряжения 220 В 400 Вт](https://www.ozon.ru/product/ptc-nagrevatel-keramicheskiy-postoyannoy-temperatury-vysokogo-napryazheniya-220-v-400-vt-2164837347)
6. [Термистор 100k 3950. можно 2 шт](https://aliexpress.ru/item/1005006645736045.html)
7. Вентилятор 4010 5V
8. [вплавляемые гайки 100PCS, M3xL4xOD4.5](https://aliexpress.ru/item/1005006079067094.html)
9. винты м4х40(8шт) с гайкой(8 шт)
10. [Провода 24AWG](https://aliexpress.ru/item/1005004336218242.html)
11. Прямые руки(опционально)
12. Много желания(обязательно)

## Модели для печати.

1. [Упоры для колпака. Используются при профилактических работах при необходимости работы с заправкой филамента.](/files/cap_stop_v2.stl)
2. [Корпус нагревателя камеры](/files/chamber_heater_v16.stl) разделить на модели в слайсере и расставить перед печатью.
3. [Панели задней крышки для установки кулеров распечатать 2 шт](/files/back_kolpak_half.stl)
4. [Жалюзи кулеров](https://www.printables.com/model/9054-gravity-vent-for-enclosure-for-120mm-fan)
5. Разьем магнитного соединения контактов крышки
6. [Задняя крышка корпуса головы экструдера](/files/backcover.stl)
7. [Чертеж для сверления отверстий в задней панели](/files/holes_v16_mirror.pdf)

## Сборка

Я попробовал распечатать черным абс и понял что на фото сборки будет черное на черном. Поэтому для мануала специально распечатал из светлого абс чтобы было виднее там где это возможно. 

### корпус нагревателя



1. Используя вплавляемые втулки собираем корпус.



не забываем про обратную сторону



1.2. Коммутируем нагреватель и реле. По фото легко понять как.



2. Коммутация предполагает 2 варианта с биметаллическим датчиком автоотключения или с монтажом термистора подключаемого к плате доп MCU.



2.1. Прикручиваем улитку кулера. для красоты немного по другому протаскиваем провод 



Подключаем остальные провода



Подключение проводов к блоку питания принтера на фото



Сверяемся или записываем куда подключаем. Картинка с пинами нам в помощь:



**Power Input** - наше питание 24 Вольта от блока питания.

**PA0** - Провод на реле нагревателя

**PA1** - Провод на улитку кулера нагревателя

**PA3** - Проводка на кулеры охлаждения установливаемые в крышку принтера

**PA5** - Термистор нагревателя. необязательный но желательный. если у вас нагреватель с биметалическим датчиком, то вам не нужен.

**PA6** - термистор камеры принтера. основной.

3. Для крепления к задней стенке используем [**шаблон**](/files/holes_v16_mirror.pdf) для сверления задней стенки корпуса 

Распечатаем и наносим на край малярный скотч как показано на фото.



Аккуратно располагаем на задней стенке в упор к левому нижнему краю и сверлим по намеченным отверстиям. Вы же вплавили с обратной стороны гайки?



Я сверлил сверлом диаметром 4.5мм чтобы был припуск на неправильную печать или кривые руки. Мне повезло - все совпало.



прикручиваем корпус нагревателя.

4. Для удобства монтажа и коммутации крышку на доп мсу не торопитесь прикручивать, это можно сделать уже после того как убедитесь что всё работает.
5. Провод USB-Mini-Usb(не торопитесь покупать пока не приехала плата, есть отзывы что может быть как **Type-C** так и **Mini-USB**) длиной минимум 1.5м лучше 1.8м необходимо провести от 
экрана через отвестие для проводов потом внутри правой стойки принтера, и далее внутри правой нижнего профиля до задней стенки.
6. Термистор камеры я закрепил на двусторонний скотч над нагревателем. 



Второй термистор у меня прикасается к самому нагревателю и служит исключительно для моего спокойствия и справочных сведений, однако в конфиге указано что если он вдруг нагреется выше 140 градусов принтер отключится.

### установка задней панели на колпак
1. Снимаем заднюю панель с родного колпака и прикручиваем распечатанные модели с отверстиями под кулеры.
2. на кулерах есть стрелка куда они будут дуть, поглядывая на нее скручиваем винтами м4х40 с гайкой(8 шт) корпус кулер и корпус жалюзи.
3. используя винты которые являлись транспортировочными для боковых стоек оси зет(вы же их не выкинули, да?) заменяем ими боковые нижние винты и прикручиваем боковые упоры. Нужны 2 гайки м4.

4. коммутируем проводку с магнитным разьемом. (модель держателя в разработке) и соединяем с платой внутри корпуса нагревателя. 

### Замена задней крышки печатающей головы

При нагреве воздуха внутри камеры принтера начинает хуже охлаждаться плата управления находящаяся внутри нашей головы. Чтобы исправить это нам придется установить дополнительный кулер. коммутируется он в паралель кулеру охлаждения радиатора хотенда(временно, изыскивается возможность подключить к задней плате.) Корпус желательно распечатать из высокотемпературного пластика, подойдут:
1. PA-СF или PA-GF 
2. ABS-CF ABS-GF
3. на крайний случай ABS или HIPS

*Вообще расположение чипа Mcu_nozle вне моего понимания логики. Мало того, что сзади, так еще и развернут лицом к корпусу мотора, ни радиатор поставить ни обдуть нормально.*

### Настройка

1. Скачиваем файл [heater.cfg](/files/heater.cfg) и помещаем в папку конфигов принтера.

2. Открываем файл printer.cfg и вписываем в произвольном месте с новой строки

`[include heater.cfg]`

3. Также для правки меню экрана нам надо добавить несколько строк в файл `/usr/data/guppyscreen/guppyscreen.json`

    * Хорошим правилом на будущее будет скачать оригинальный файл на всякий случай. можно создать бекап командой

    ```
    cp /usr/data/guppyscreen/guppyscreen.json /usr/data/guppyscreen/guppyscreen.json.backup
    ```



```
,
    {
      "display_name": "back_fans",
      "id": "fan_generic back_fans"
    },
    {
      "display_name": "Chamber",
      "id": "fan_generic chamber"
    }
```

и ищем следующие строки по картинке и вставляем аналогично первому примеру.



```
,
    {
      "color": "blue",
      "controllable": true,
      "display_name": "Chamber",
      "id": "heater_generic Heater_TT"
    },
    {
      "color": "green",
      "controllable": true,
      "display_name": "Blower_Fan",
      "id": "temperature_fan blower_fan"
    }
```

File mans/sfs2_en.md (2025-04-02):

# Installing SFS 2.0 Instead of Standard Filament Runout Sensor

## Why Upgrade?
Given the Ender 5 Max's large build volume, extended print times, and high filament consumption, basic runout detection alone is insufficient. The cost of filament jams can be exceptionally high, making a system that monitors both runout and movement an excellent solution.

This upgrade minimizes failure risks and prevents material/time losses.

## Wiring Options
Since standard sensors use 3 wires while SFS 2.0 uses 4, there are two installation methods:

### Method 1: Basic Replacement (No Additional Wiring)
Replaces only the movement detection functionality while maintaining the same wiring:

1. Repin the connector to 4-wire configuration:

## 2. Electrical Connection

| Sensor Cable | Ender 5 Max Connection |
|---|---|
| Red (+5V) | 5V Power |
| Black (GND)  | Ground |
| Green (SIG)  | PC6 (Signal) |
---------------------------------------

> **Note:** Verify polarity before connecting!





in `printer.cfg` find and remove this

```
[filament_switch_sensor filament_sensor] 
switch_pin: !PC6
pause_on_runout: true
```

Add to `printer.cfg`:

```
[filament_motion_sensor filament_sensor]
detection_length: 5.3
extruder:extruder
pause_on_runout: true
switch_pin: ^PC6
runout_gcode:
  RESPOND TYPE=command MSG="Filament runout/blocked!"
insert_gcode:
  RESPOND TYPE=command MSG="Filament inserted"

```
### OR use with Optional audio alerts:

```
[gcode_shell_command beep]
command: beep
timeout: 2
verbose: False

[gcode_macro BEEP]
description: Play a sound
gcode:
  RUN_SHELL_COMMAND CMD=beep

[filament_motion_sensor encoder_sensor]
switch_pin: ^!PC6
detection_length: 5.3 # возможно сделать чуть меньше 2.7 по умолчанию
extruder: extruder
runout_gcode:
  RESPOND TYPE=command MSG="Filament runout/blocked!"
  UPDATE_DELAYED_GCODE ID=sfs_alarm DURATION=1
insert_gcode:
  RESPOND TYPE=command MSG="Filament inserted"
  UPDATE_DELAYED_GCODE ID=sfs_alarm DURATION=0

[delayed_gcode sfs_alarm]
# initial_duration: 0
gcode:
  beep
  beep
  beep
  beep
  beep
  beep
  # UPDATE_DELAYED_GCODE ID=sfs_alarm DURATION=1  # Uncomment for continuous alarms
```
## Method 2: Full Functionality (With Additional Wiring)
For complete sensor capabilities with reduced false positives:

1. Extend the 4th wire (blue) to motherboard:

Connect to available GPIO (PA15 shown)



Use proper wire extensions if needed

2. Update `printer.cfg` find and remove this

```
[filament_switch_sensor filament_sensor] 
switch_pin: !PC6
pause_on_runout: true
```

Add to `printer.cfg`:

```
[gcode_shell_command beep]
command: beep
timeout: 2
verbose: False

[gcode_macro BEEP]
description: Play a sound
gcode:
  RUN_SHELL_COMMAND CMD=beep

[filament_switch_sensor filament_sensor]
switch_pin: PA15
pause_on_runout: true
# runout_gcode: PAUSE

[filament_motion_sensor encoder_sensor]
switch_pin: ^!PC6
detection_length: 5.3
extruder: extruder
runout_gcode:
  RESPOND TYPE=command MSG="Filament runout/blocked!"
  UPDATE_DELAYED_GCODE ID=sfs_alarm DURATION=1
insert_gcode:
  RESPOND TYPE=command MSG="Filament inserted"
  UPDATE_DELAYED_GCODE ID=sfs_alarm DURATION=0

[delayed_gcode sfs_alarm]
# initial_duration: 0
gcode:
  beep
  beep
  beep
  beep
  beep
  beep
# UPDATE_DELAYED_GCODE ID=sfs_alarm DURATION=1  # Uncomment for continuous alarms
```

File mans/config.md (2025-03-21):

<h2>Исправления конфигурации принтера для большей функциональности.</h2>

открываем printer.cfg

 1. найдем раздел  `[printer]`

```
[printer]
kinematics: corexy
max_velocity: 800
max_accel: 20000
max_accel_to_decel: 10000
max_z_velocity: 30
square_corner_velocity: 5.0
max_z_accel: 300

```
исправив его данным образом уйдем от неправильных значений максимальных ускорений изза которых при неправильных настройках слайсера мы можем повредить принтер.

 2. после этого раздела добавим строку:

```
[exclude_object]

```
Это добавит функционал исключения объектов, крайне востребованная функция для принтеров с таким размером рабочего стола.

 3. в разделе `[adxl345]` строка `axes_map: x,-z,y` точно неправильная, но пока не выяснил как записать правильно. 

 4. Лампочка состояния принтер, по отзывам, горит слишком ярко. Исправим это: ищем следующие разделы и меняем как написано тут. также исправляем логику подсветки стола которая была инвертирована.

 ```
[output_pin green_pin]
pin: PA0
pwm: True
cycle_time: 0.010
value: 0
[output_pin red_pin]
pin: PC1
pwm: True
cycle_time: 0.010
value: 0
[output_pin yellow_pin]
pin: PA1
pwm: True
cycle_time: 0.010
value: 0.01
[output_pin light_pin]
#pin: nozzle_mcu: PB0 #PA10
pin: !PC0
pwm: True
cycle_time: 0.010
value: 1.0
 ```
 5. Чтобы алгоритмы отрабатывали правильно нам необзодимо также исправить файл `gcode_macro.cfg` заходим туда и находим следующие разделы и меняем их на представленные ниже

```
###YINZHI
[gcode_macro RED_LED_ON]
gcode:
  SET_PIN PIN=red_pin VALUE=1

[gcode_macro RED_LED_OFF]
gcode:
  SET_PIN PIN=red_pin VALUE=0

[gcode_macro GREEN_LED_ON]
gcode:
  SET_PIN PIN=green_pin VALUE=0.02

[gcode_macro GREEN_LED_OFF]
gcode:
  SET_PIN PIN=green_pin VALUE=0

[gcode_macro YELLOW_LED_ON]
gcode:
  SET_PIN PIN=_yellow_pin VALUE=0.01

[gcode_macro YELLOW_LED_OFF]
gcode:
  SET_PIN PIN=yellow_pin VALUE=0

[gcode_macro LIGHT_LED_ON]
gcode:
  SET_PIN PIN=light_pin VALUE=1

[gcode_macro LIGHT_LED_OFF]
gcode:
  SET_PIN PIN=light_pin VALUE=0
```
красный я оставил без изменений чтобы чтобы при ошибке привлечь ваше внимание. однако вы можете поменять яркость и на нем. 

 6. Решив сделать принтер чуть тише я изменил логику работы кулера материнской платы, теперь он срабатывает при включении мотора икса. 
```
#############FAN OLD CONFIG
#[output_pin MainBoardFan] # закоментируйте этот раздел
#pin: !PB1

[controller_fan MCU_fan] # включаем обдув после включения драйверов
pin: PB1
max_power: 1.0
fan_speed: 1
kick_start_time: 0
stepper: stepper_x
```
в данном примере вы видите что вам надо закоментировать и что добавить.

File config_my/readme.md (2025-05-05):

<h3 align="right"><a href="https://www.tinkoff.ru/rm/yakovleva.irina203/51ZSr71845" target="_blank">ваше "спасибо" автору</a></h3>
<h3 align="right"><a href="https://t.me/tombraider2006" target="_blank">телеграм канал автора</a></h3>

<h2>мой конфиг</h2>

# на данный момент это руководство носит справочный характер и не является руководством к действию. 

[**english version**](/config_my/readme_en.md)

Данный конфиг после! установки хелпер скрипта с моими правками. 

Если вы хотите повторить то сначала необходимо 

1. установить [хелпер скрипт](https://guilouz.github.io/Creality-Helper-Script-Wiki/helper-script/helper-script-installation/)
2. установить пункты 1 2 4 5 6 7 

читайте [руководство](/firmware.md) 

как может выглядеть интерфейс после установки.

https://github.com/user-attachments/assets/1851a861-b29d-4a3b-ac2f-7861f6cc0bae

Выложен для ознакомления и обсуждения.


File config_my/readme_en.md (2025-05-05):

<h2>My config</h2>

This config after! installing the helper script with my edits.

If you want to repeat, then first you need to

1. install [helper script](https://guilouz.github.io/Creality-Helper-Script-Wiki/helper-script/helper-script-installation/)
2. install the items that are marked with green checkmarks. 1 2 4 5 6 7.



What the interface might look like after installation.

https://github.com/user-attachments/assets/1851a861-b29d-4a3b-ac2f-7861f6cc0bae

Posted for review and discussion.

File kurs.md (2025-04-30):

<h3 align="right"><a href="https://www.tinkoff.ru/rm/yakovleva.irina203/51ZSr71845" target="_blank">ваше "спасибо" автору</a></h3>
<h3 align="right"><a href="https://t.me/tombraider2006" target="_blank">телеграм канал автора</a></h3>

## О КУРСЕ
Этот курс – необходимый компаньон для тех, кто только начинает свой путь в мире 3D-печати. Чтобы не утонуть в океане информации требуется наставник, способный ориентировать вас в огромном объеме материалов.

Именно здесь я приду к вам на помощь, предлагая не только основы, но и ключевые ссылки на актуальные и релевантные источники.

Мой курс разработан так, чтобы помочь вам быстро освоить все тонкости работы с 3D-принтерами, предоставив полезные сведения и сократив путь к вашему профессиональному росту.  

настроим слайсер, на принтер поставим модифицированную прошивку со всеми новыми наворотами. 

 1. Установка модификаций ПО. 2 варианта: SimpleAF\Helper Script
 2. Тонкая настройка конфигурационных файлов принтера
 3. Пояснение принципов работы и каждого изменения от стокового ПО
 4. Обьяснение нюансов интерфейса веб панели и его практического применения
 5. Советы по регулярному обслуживанию принтера.
 6. Cоветы по исправлению наклона стола.
 7. Интерфейс слайсера и настройка под принтер.
 8. Объяснения настроек параметров пластика.
 9. Порядок тестов настройки параметров пластиков и нюансы проведения тестов.
 10. Пробная печать, пояснения особенностей алгоритмов работы. на том пластике который у вас есть(pla, petg, ABC)
 11. Ответы на вопросы по печати.

 в общем  провожу вас за ручку в мир качественной быстрой печати. 
записаться можно тут(пишите ник в телеграмме и вариант прошивки SimpleAF\Helper Script ) https://easyweek.ru/tom-tomich

https://youtu.be/q9dPGSkCr6M?si=31thqjn6EUDBIXiD

Отзыв на обучение.

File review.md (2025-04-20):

Первые впечатления от принтера.

1. Коробка огромная и тяжелая. 31 кг. Надежно, мощно. сильно. понравилось.

2. Сборка достаточно легкая. посмотрел [видео](https://youtu.be/VDOPQRVCY3I?si=ck5SxVFJXiyOnVK2) также в комплекте инструкция по сборке. все болтики в отдельных пакетиках, подписаны. удобно.

3. Первое включение долгое. пока тест пройдет, по сравнению с к серией стол поднимается и опускается медленно, но это не страшно. 

4. размеры указанные на сайте пугают но на самом деле размеры самого металлического кубика 608х608х625 остальное это выступающие части типа экрана спереди датчика филамента и держалки пластика справа и сверху держатель кабелей идущих к голове.

карта стола в стоке при нагреве до 45 градусов выглядит так:

 

Однако первый слой почти не подкачал и выглядит очень прилично а уж для стола 400на400 так вообще прекрасно:





3 График потребления электроэнергии для стола в 45 градусов и хотенда 220 вполне себе на уровне.



 Не забываем о том, что грелка стола тут 1000 ватт и хотенд выглядит тоже весьма впечатляюще. 



сопло тут свое, специфическое. похоже на мк8 но с более длинным носиком.

 Хотенд при тестах спокойно выдавал 30 мм кубических. на 35 возникали небольшие дефекты но кратковременно можно разгонять и до него. 

 

4 немного фото как выглядит меню. Сразу напишу - на данный момент доступа root нет.(уже есть) 















Почти ничего нового для пользователей креалити, доступ к облачным сервисам как всегда работает из коробки.

Из  опыта, продавливание нового филамента лучше повторять раза три, изза того что объем хотенда стал значительно больше, цвет может долго перемешиваться с предыдущим. 

Хорошим подспорьем будет [Камера Creality Nebula](https://aliexpress.ru/item/1005006159528565.html) насколько хорошо будет отрабатывать ИИ еще неизвестно но и без этого штука полезная  для контроля за печатью.

## update. 

После получения root отвечая на вопрос насколько "ужасно" печатает принтер в стоке. 

1. креалити как всегда пытаются загнать под ковер конкретные значения искривления  стола, когда печатаем много мелких деталек это не страшно но если начнем печатать большую деталь которая будет сопрягаться с другой большой деталью это может вылиться в очень большую проблему.
2. отсутствие исключения моделей представляет проблему уже при печати много мелких моделей.
3. тензы стола работают не то чтобы идеально, мне повезло и у меня с первого дня обрабатывался стол вполне неплохо(по сравнению с к1) однако если сравнивать с нептуном 4 макс(на секундочку в 2 раза дешевле) то там первый слой мне понравился больше.  не забываем о том что инструментов для правки стола нам креалити не предоставила.
4.  `variable_autotune_shapers: ei` уж сколько раз твердили миру...  принудительное ограничение выбора шейперов никак не улучшает качество печати а скорее вредит.
5. Нет стартового и конечного кода, нет KAMP. 

6. По отзывам пользователей одна из самых больших проблем стоковой прошивки это ошибка которая при паузе на слое при вовращении делает ошибку высоты возвращения.  

на данный момент одна из самых допиленных версий прошивок это от pelkorp с его [**SimpleAF**](https://pellcorp.github.io/creality-wiki/).

[**Установка на русском прошивки SimpleAF**](/mans/simpleaf.md)  К ее недостаткам можно отнести только что поставить можно !!!только на картографер и бекон. связано это с тем что не смогли с новым клиппером плату головы а точнее акселерометр. так как в картографере и беконе внутри плат есть акселерометры свои, вышли из положения таким образом.  Вполне возможно что через некоторое время ситуация измениться.  

я также перепиливаю прошивку и добавляю возможности к стоковой конфигурации. так как круг пользователей пока небольшой комьюнити не такое активное как хотелось бы.

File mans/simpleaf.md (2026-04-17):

## Установка прошивки Simple Af Ender 5 Max

### Почему Simple AF

Данная модификация призвана решить несколько проблем существующих на стоковой прошивке и не устранимых даже с модификациями Helper Script.

Долгий старт и долгое, неточное тестирование первоначальный тест Z оси, очистка сопла, "круг почета" тестирования тензодатчиков. В прошивке Simple Af родные тензодатчики не задействованы вместо них предлагается использовать альтернативы.

Отсутсвие алгоритма KAMP в стоковой прошивке изза чего стол тестируется долго, неточно, и не только где нам надо, а везде.

Осталость от современных тенденций развития алгоритмов Алгоритм input shaping, adaptive mesh, и еще многое получило свое развитие, в отличии от прошивки которая находится в том же состоянии что и несколько лет! назад. Косметические улучшения не устранили отставание, а где то и привнесли новые проблемы например жесткая привязка к Creality Print после прошивки 1.2.0.20

Всё это мы вынуждены терпеть из-за выбора компанией Creality собственного пути развития датчиков оси Z который разошелся с основной веткой klipper.

Немного с сайта прошивки о плюсах данного решения.

*Открытый исходный код Simple AF использует программное обеспечение с открытым исходным кодом, и весь его исходный код открыт.*

*Простая конфигурация Все макросы и конфигурации находятся в каталоге config и доступны вам, ничего не заперто в закрытых исходных кодах.*

*Обновленный Клиппер Используемая нами версия klipper, хотя и является ответвлением от основной версии, регулярно обновляется с помощью klipper3d, и никакие наши добавления не меняют базовое поведение klipper.*

Основная проблема в том что обновленный klipper прошивки не может использовать родные тензодатчики стола. от них придется отказаться и одним из самых продвинутых вариантов является картографер с которым мы и будем дружить наш принтер. Для начала нам необходимо получить доступ к консоли линукс и для этого нам необходимо установить предустановленную прошивку от [zevaryx](/firmware.md) что даст нам возможность зайти по ssh с правами root.

Далее нам надо подготовить печатные детали креплений датчика картографер и экрана:

### Варианты креплений датчика

| Модель | Тип | Ссылка | Примечания |
|---|---|---|---|
| SimplyHexed  | Прямой угол 90 | [Printables](https://www.printables.com/model/1209230-ender-5-max-simply-hexed) | Только для Ender 5 Max |

Если меняли хотенд на к2 то необходим [корпус обдува уменьшенный по высоте на 2 мм](/files/front_cover_carto.stl) 

### Крепление экрана

Так как в прошивке SimpleAF используется горизонтальное положение экрана используем [**такую**](/files/Ender5MaxScreenMount.stl) модель крепления.

### Прошивка датчика

К сожалению  прошить датчик непосредственно с принтера не получится. так как на принтере хоть и линукс но чильно кастрированный, придется использовать костыли в виде LiveUSB с например ubuntu

На датчике должна быть установлена прошивка не старше `CARTOGRAPHER K1 5.1.0` : 

[**Инструкции по прошивке датчика**](https://pellcorp.github.io/creality-wiki/cartographer_flashing/)

[**Инструкции по прошивке датчика в среде windows. WSL Hack**](/mans/wsl.md) прошивка с помощью встроенного в windows linux

#### Ошибки при прошивке

проверить  что датчик виден в системе всегда можно командой `ls /dev/serial/by-id/*` если  система не находит ничего - проверьте соединение. Иногда путают местами провода передачи данных (зеленый и белый) их можно попробовать поменять местами



если все хорошо то система должна выдать результатом команды `ls /dev/serial/by-id/*` что то похожее на `/dev/serial/by-id/usb-Klipper_stm32f042x6_120031001653304B4D323431-if00` *это пример! не используйте*

В дальнейшем эта строку скрипт установки использует в файле `cartotouch.cfg`  для определения устройства и выглядеть она будет как то так:

```
[scanner]
is_non_critical: true           # flag this as non critical
serial: /dev/serial/by-id/usb-Cartographer_614e_28001D00124330394D363620-if00
```

### Подготовка и прошивка.

Чтобы убедится что нам ничто не помешает и не останется ничего лишнего сбросим прошивку до заводских однако сохраняя доступ и настройки wifi для этого скопируйте данны код и вставьте в консоль:

```
wget --no-check-certificate https://raw.githubusercontent.com/pellcorp/creality/main/k1/services/S58factoryreset -O /tmp/S58factoryreset
chmod +x /tmp/S58factoryreset
/tmp/S58factoryreset reset

```
Очень важно не закрывать сеанс SSH, пока не получите следующее сообщение:

`Info: Executing factory reset... Info: Factory reset was executed successfully, the printer will restart...`

принтер перезагрузится и можно переоткрыть консоль ssh.

### Важно! проверьте дату на принтере.

```
date
```
если отличается от текущей 

```
hwclock -w
```
и еще раз проверяем

```
date
```
**вариант номер 2.**

 просто выставьте текущий часовой пояс на принтере.

если этого не сделать то будет ошибка в сертификатах и модули установочные не загрузятся.

Далее клонируем репозиторий с прошивкой:

```
git config --global http.sslVerify false
git clone https://github.com/pellcorp/creality.git /usr/data/pellcorp
sync

```
**Альтернативный сервер** если идут ошибки по недоступности изза РКН

```
git config --global http.sslVerify false
git clone https://tomich.fun/git/creality.git /usr/data/pellcorp
sync
```

### Запускаем установщик

```
/usr/data/pellcorp/installer.sh --install cartographer --mount SimplyHexed

```

установка займет какое то время. 

### После установки

Возможное обновления прошивки MCU

Если в конце процесса установки вы получите следующее сообщение:

`WARNING: MCU Firmware updates are pending you need to power cycle your printer!`

Это означает, что необходимо применить новые обновления прошивки MCU, и это можно сделать только путем выключения и повторного включения принтера. После выключения и повторного включения принтера вы можете проверить, была ли обновлена прошивка с помощью `CHECK_FIRMWARE` макроса из Fluidd, если вы видите это сообщение: `INFO: Your MCU Firmware is up to date` значит все нормально.

После прошивки на экране принтера будет запрос на калибровку экрана. не игнорируйте его.

### Калибровка

Для настройки нового принтера необходимо выполнить три различных шага калибровки: 

<details><summary>Ручная калибровка  картографа<small><i><red> нажми чтобы раскрыть список</red></i></small></summary>

Следующие команды вводим в консоли вебпанели.

1. Делаем хоум осей икс игрек  XY  `G28 X Y`
2. Нагрейте сопло до 150 °C  `M109 S150`.
3. Убедитесь, что сопло расположено по центру кровати.
4. Выполните  `CARTOGRAPHER_SCAN_CALIBRATE` бумажный тест. Не используйте металлический щуп на этом этапе, он может помешать калибровке!!!
5. После окончания нажмем сохранить перегрузить или введем в панели `SAVE_CONFIG` </details>

<details><summary>Картографическое пороговое сканирование<small><i><red> нажми чтобы раскрыть список</red></i></small></summary>

**На этом следующем этапе очень важно находиться рядом с принтером, поскольку если возникнут какие-либо проблемы с конфигурацией принтера или зондом картриджа, сопло может застрять в платформе, поэтому держите руку над кнопкой аварийной остановки!**

Следующие команды вводим в консоли вебпанели.

1. Делаем хоум Всех осей `G28`
2. Убедитесь, что сопло расположено по центру кровати.
3. Нагрейте сопло до 150 °C `M109 S150`
4. Выполнить `CARTOGRAPHER_TOUCH_CALIBRATE`
5. по завершении `SAVE_CONFIG`
</details>

В родном мануале далее рекомендуется выполнить калибровку компенсации скручивания оси, но так как у нас в креплении нет сдвига по обоим осям нам это необязательно. 

если ваша карта стола выглядит так:



то вы забыли прошить сам картографер и вам придется всю настройку повторить заново после прошивки.

 Если вы запускаете калибровку для принтера, который был откалиброван ранее, перед повторным выполнением этих калибровок необходимо удалить следующие разделы SAVE_CONFIG :
```
[scanner model default]
[scanner]
[axis_twist_compensation]
[bed_mesh]

```

### Наладка прошивки.

Для начала сделаем несколько тестов и калибровок.

Следующие команды вводим в консоли вебпанели.

```
PID_CALIBRATE_BED BED_TEMP=65
PID_CALIBRATE_HOTEND HOTEND_TEMP=230
INPUT_SHAPER
SAVE_CONFIG
```

`PID_CALIBRATE_HOTEND HOTEND_TEMP=230` и `PID_CALIBRATE_BED BED_TEMP=65` это процедура калибровки, которая гарантирует, что принтер всегда будет поддерживать стабильную заданную температуру . PID (пропорционально-интегральная производная) используется в принтерах для поддержания стабильной температуры в хотенде и\или нагреваемом столе.

`INPUT_SHAPER` делает тест резонансов и записывает результат в `printer.cfg`

по завершении `SAVE_CONFIG` сохранит все наши данные в файле `printer.cfg` и перезапустит принтер. 

Также можно запустить `INPUT_SHAPER_GRAPHS` чтобы посмотреть графики резонансов. после теста они появятся в корневой папке конфигов.  

`BELTS_SHAPER_CALIBRATION` делает тест резонансов и создает график натяжения ремней.

## Правка начального и конечного кода слайсера.

В современных принтерах давно ушли от начальных g-code в слайсере и применяются макросы которые на старте печати сверяясь с различными условиями гораздо эффективнее подготавливают принтер к печати. чтобы пользоваться этими современными методами в нашей прошивке достаточно поставить правильные стартовый и конечный код в слайсере. 

так как мы используем откат из прошивки нам необходимо подправить несколько пунктов:





стартовый код для **OrcaSliser**:

```
M140 S0
M104 S0
START_PRINT EXTRUDER_TEMP=[nozzle_temperature_initial_layer] BED_TEMP=[bed_temperature_initial_layer_single]
SET_RETRACTION RETRACT_LENGTH=[retraction_length] RETRACT_SPEED=[retraction_speed] UNRETRACT_EXTRA_LENGTH=[retract_restart_extra] UNRETRACT_SPEED=[deretraction_speed]
RESPOND TYPE=command MSG="Retraction length set to [retraction_length]mm" 
RESPOND TYPE=command MSG="Retract speed set to [retraction_speed]/[deretraction_speed]mm/c"

```

конечный код для **OrcaSliser**:

```
END_PRINT

```
 если после установки Simple AF печатает не пойми как и летят "Unknown command G2, G3, G10, G11", то вставить прям в printer.cfg куда-нибудь в конец это:

 ```
[gcode_arcs]

[firmware_retraction]
retract_length: 0.45 # безопасное значение для того пластика которым чаще всего печатаете.
retract_speed: 30
unretract_extra_length: 0
unretract_speed: 30

 ```

### вы купили зашивку корпуса и теперь провода мешают открывать дверцу.

Вот [**модель**](/mans/Ender5MaxTiltedScreenMount.stl) чтобы закрепить экран в горизонтальном положении. 



### Смена ориентации экрана:

1. в файлах флюида находим grumpyscreen.ini

в нем ищем параметр:

`"display_rotate": 2,` - находим строку и меняем значение на 0.

2. **Перезагружаемся и проводим калибровку экрана.**



Вы можете обратиться ко мне за [**консультацией**](/kurs.md). и я помогу с установкой програмного обеспечения.

## Разное полезное

чтобы принтер не шумел обдувом материнской платы при простое.

в файле `fan_control.cfg` **надо заменить** раздел `[static_digital_output mcu_fan_always_on]`. старый стираем этот вставляем.

```
[controller_fan MCU_fan] # включаем обдув после включения драйверов
pin: PB1
max_power: 1.0
fan_speed: 1
kick_start_time: 0
stepper: stepper_x

```

в файле `start_end.cfg` ищем макрос `[gcode_macro _CLIENT_VARIABLE]`

в нем в строке меняем 25 на 380чтобы стол отьезжал ниже. *полезно тем у кого принтер стоит выше чем на полу*

```
variable_custom_park_dz: 380.0 # положение стола после печати
```
по просьбам еще немного перевода из макроса `[gcode_macro _CLIENT_VARIABLE]`

```
[gcode_macro _CLIENT_VARIABLE]
variable_park_at_cancel: True # не трогаем
variable_use_custom_pos: True # не трогаем
variable_custom_park_dz: 380.0 # позиция по Z при отмене или завершении печати
variable_park_at_cancel_x: 396 # позиция по X при отмене или завершении печати
variable_park_at_cancel_y: 391 # позиция по Y при отмене или завершении печати
variable_cancel_retract: 7.0 # втягивание филамента при отмене или завершении печати
variable_custom_park_x: 300 # позиция по X при паузе, смене филамента или его окончании
variable_custom_park_y: 9 # позиция по Y при паузе, смене филамента или его окончании
variable_retract: 1.0 # значения ретракта по умолчанию
variable_speed_retract: 35.0 # скорость ретракта в мм/с
variable_unretract: 1.0 # скорость возврата филамента в мм/с
variable_speed_unretract: 35.0 # скорость возврата подачи филамента в мм/с
variable_speed_hop: 15.0 # скорость движения по оси Z в мм/с
variable_speed_move: 100.0 # скорость перемещения в мм/с
variable_user_cancel_macro: "_ON_CANCEL" # не изменять — отвечает за отмену печати
variable_user_resume_macro: "_ON_RESUME" # не изменять — отвечает за возобновление после паузы
variable_user_pause_macro: "_ON_PAUSE" # не изменять — отвечает за выполнение пользовательского кода при паузе

```

если не хочется ждать стабилизации температуры перед печатью ставим 0 в следующем макросе:

```
[output_pin Bed_Warp_Stabilisation]
pin: virtual_pin:BED_WARP_STABILISE_pin
value: 0

```

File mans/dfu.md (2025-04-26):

Прошивка картографера для Windows (на данный момент работоспособность не доказана. через линукс по факту проще)

## Вход в режим DFU

Вход в режим DFU может быть немного затруднительным, но как только вы освоитесь, все станет довольно просто.

Подключите USB-кабель к ПК с ОС Windows, с которого вы будете производить прошивку, и к датчику Cartographer. 

Используя пинцет из железа или аналогичный инструмент, соедините контакты 1 (boot0), как только на них будет достигнут прочный контакт, коснитесь контакта 2 (сброс) другим инструментом из железа.



Если вы все сделали правильно, ваше устройство должно перейти в режим DFU.

Windows — выполните следующие действия.

Меню «Пуск»

Найдите и откройте «Диспетчер устройств».

Прокрутите вниз до раздела Устройства универсальной последовательной шины.

Вы должны увидеть STM32 BOOTLOADER как опцию.



## Прошивка через STM32CubeProgrammer Windows 

скачать программу можно с [официального сайта](https://www.st.com/en/development-tools/stm32cubeprog.html) но исключительно через VPN и регистрацию. Или можно по ссылке с телеграмм группы [пользователей Ender 5 max](https://t.me/Ender_5_Max_Ru/5283)

Откройте приложение и СПРАВА выберите следующие параметры и нажмите Подключиться .



Для прошивки Cartographer вам нужно установить адрес `0x08002000` Это обеспечивает смещение в 8 КБ для прошивки. Прошивка загрузчика Katapult может быть прошита по умолчанию `0x08000000`.



На каждой прошивке нажмите "Download", начиная с Katapult, затем Cartographer. Теперь нажмите Disconnect в ВЕРХНЕМ ПРАВОМ углу.

Если мигает СИНИЙ светодиод, значит, вы не полностью обновили прошивку и вам следует начать заново. Если вы сейчас выключите и включите питание зонда или просто нажмете на контакты RESET (2), как было сделано ранее, ваш зонд должен отреагировать, если под него поместить что-то твердое металлическое.

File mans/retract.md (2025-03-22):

<h3 align="right"><a href="https://www.tinkoff.ru/rm/yakovleva.irina203/51ZSr71845" target="_blank">ваше "спасибо" автору</a></h3>
<h3 align="right"><a href="https://t.me/tombraider2006" target="_blank">телеграм канал автора</a></h3>
<h5 align="right">поставьте "звездочку" проекту. так другим пользователям легче его найти.</h5>

<h2> управляем ретрактом во время печати.</h2>

в прошивке клиппер возможно управлять ретрактом во время печати. это нужно если вы внезапно увидели, что ваш пластик отсырел и начал тянуть сопли,  а у вас уже прошло "n" часов печати и так лень все начинать заново. но для этого нужно немного подготовительной работы. 

первое. в орке заходим в настройки принтера и ставим галки "использовать откат из прошивки" 



убираем галочку очистка сопла при откате во вкладке экструдер



далее в стартовом коде принтера добавляем блок:

```
SET_RETRACTION RETRACT_LENGTH=[retraction_length] RETRACT_SPEED=[retraction_speed] UNRETRACT_EXTRA_LENGTH=[retract_restart_extra] UNRETRACT_SPEED=[deretraction_speed]
RESPOND TYPE=command MSG="Retraction length set to [retraction_length]mm" 
RESPOND TYPE=command MSG="Retract speed set to [retraction_speed]/[deretraction_speed]mm/c"
```



не забывайте вписывать значение отката для своего пластика когда настраиваете.

например так:



далее переходим в принтер и открываем файл printer.cfg

вписываем такой раздел:

```
[firmware_retraction]
retract_length: 0.43 # безопасное значение для того пластика которым чаще всего печатаете.
retract_speed: 30
unretract_extra_length: 0
unretract_speed: 30

```
после перезагрузки если вы не увидели нового раздела в правом верхнем углу тыкаем в три точки и ищем следующий раздел:



внутри находим раздел "настройки отката" и ставим галочку



В результате у нас появится новый раздел в веб панели с помощью которого вы можете прямо во время печати управлять вашим ретрактом. 



проверить все ли у вас правильно перед печатью можно нарезав модель и сохранив ее на диск, далее открываем файл с помошью текстового редактора и ищем `Move Z Axis up` 



убеждаемся что у нас есть команда **set_retraction** и то что там у нас цифры, а так же что дальше у нас есть команда **G10**  которая означает что послана команда на ретракт который будет обработан прошивкой.

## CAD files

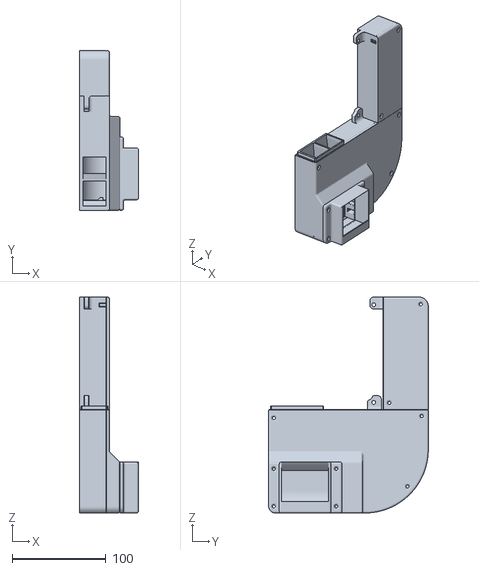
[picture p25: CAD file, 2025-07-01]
files/chamber_heater_v16.stl
62.9 x 170.0 x 230.0

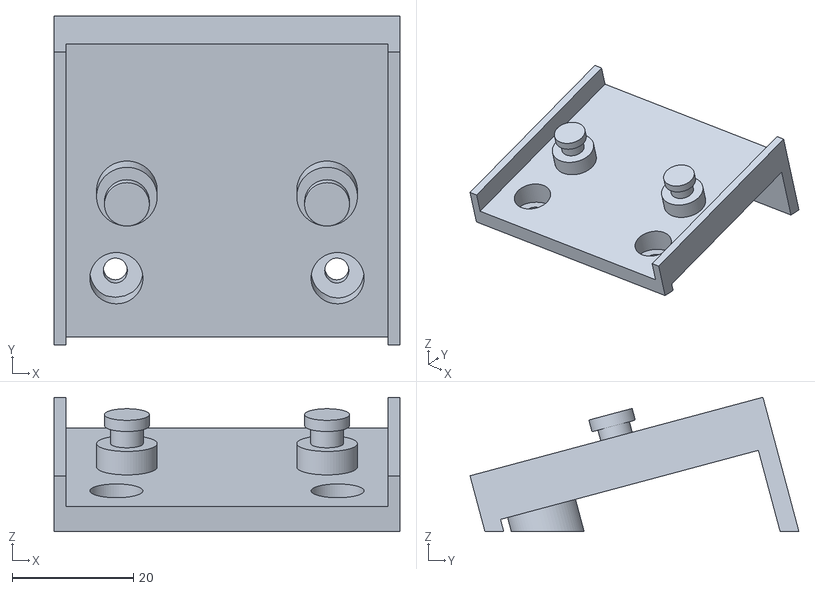
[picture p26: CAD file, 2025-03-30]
mans/Ender5MaxTiltedScreenMount.stl
57.0 x 54.2 x 22.2

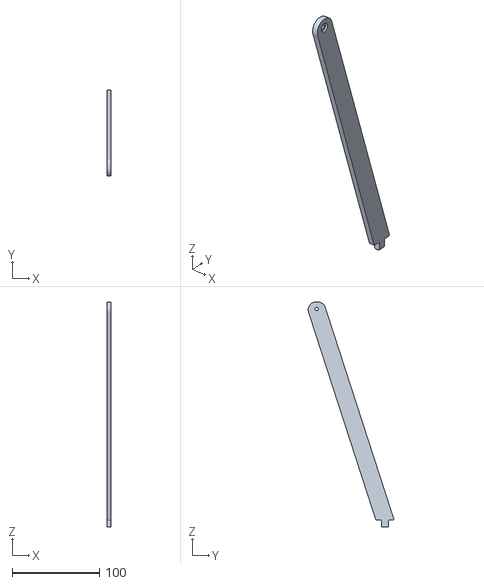
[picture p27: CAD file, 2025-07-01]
files/cap_stop_v2.stl
5.00 x 98.3 x 258.0

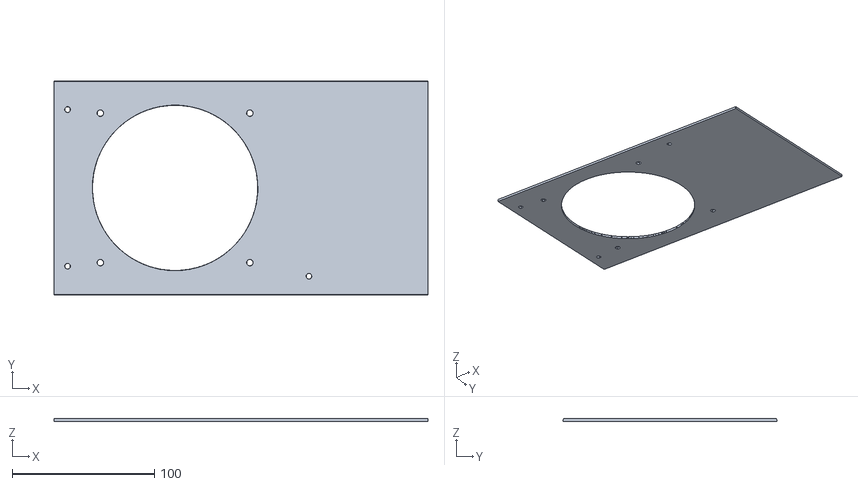
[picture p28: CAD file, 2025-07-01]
files/back_kolpak_half.stl
262.6 x 150.2 x 2.00

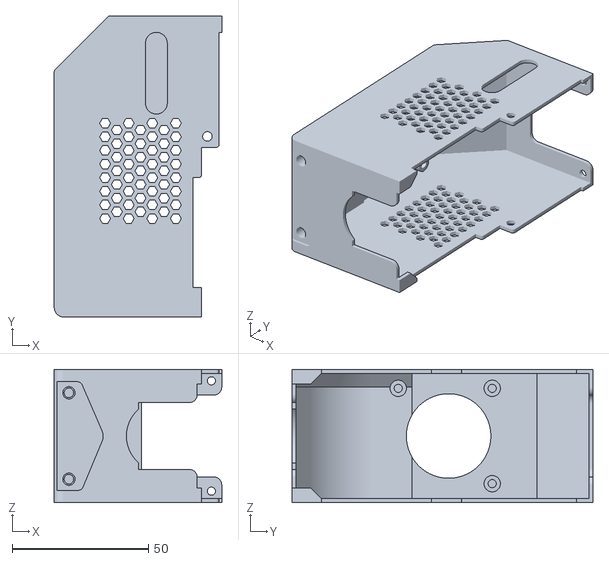
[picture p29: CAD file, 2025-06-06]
files/front_cover_head.stl
61.5 x 110.5 x 49.0

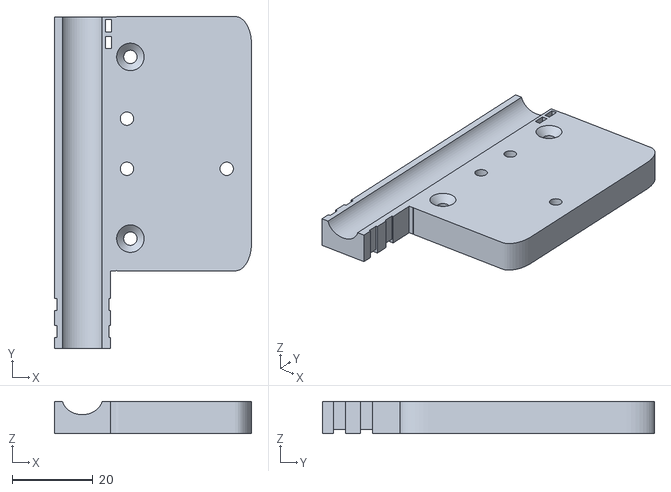
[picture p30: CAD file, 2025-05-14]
files/Ender5MaxSFSMount.stl
48.8 x 82.2 x 8.00

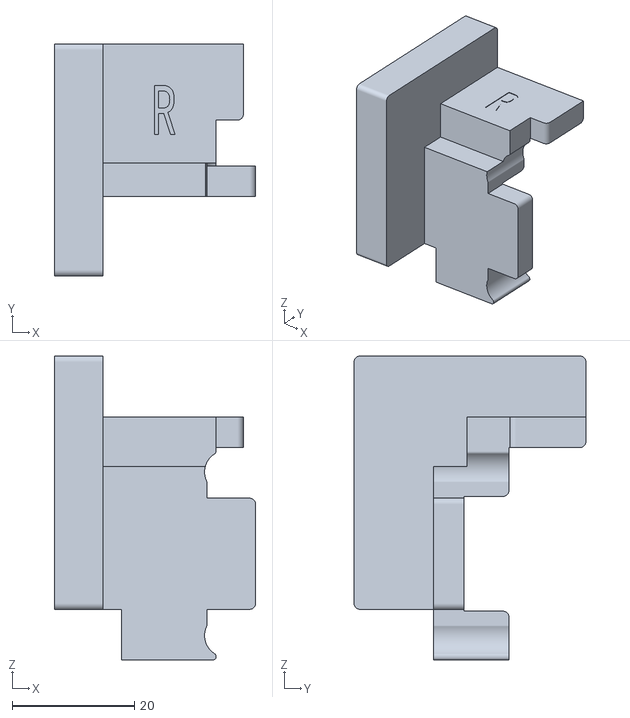
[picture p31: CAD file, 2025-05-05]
files/Y-axis+tensioning+tool-20250220.stl
33.0 x 38.0 x 49.8

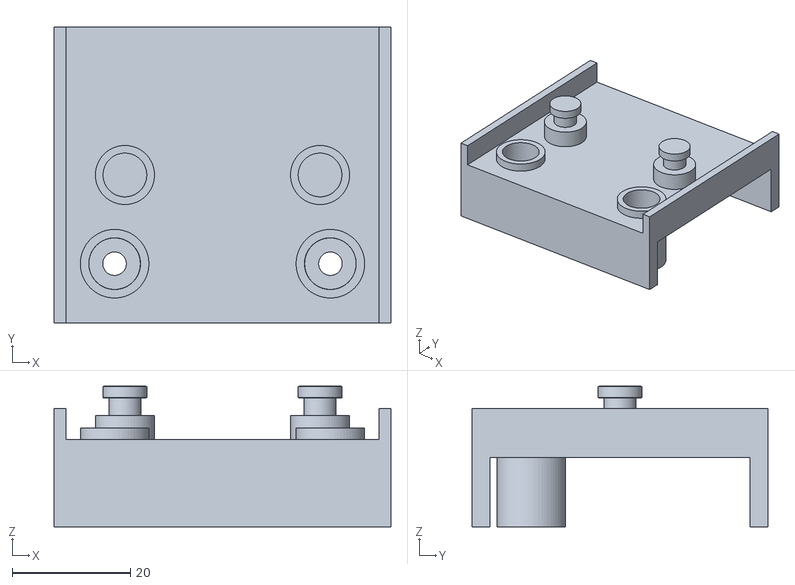
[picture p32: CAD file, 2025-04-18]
files/Ender5MaxScreenMount.stl
57.0 x 50.0 x 23.8

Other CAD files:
files/X-axis+tensioning+tool-20250220.stl

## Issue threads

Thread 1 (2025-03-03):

Source for V6.2.0.10 firmware

zevaryx, 2025-03-03:
Hi! I'm the creator of the pre-rooted firmware for the Ender 5 Max. Feel free to update the link to point to my GitHub repo, the releases contain the latest pre-rooted firmware images

https://github.com/zevaryx/ender-5-max-firmware

Tombraider2006, 2025-03-03:
Thank you for your attention. Of course, I will make a link to your repository. Taking this opportunity, I would like to ask you to describe on your resource how to return the original firmware if necessary.

zevaryx, 2025-03-03:
As of right now, I'm not sure how to return to original firmware. There's something different about the Ender 5 Max that locks out downgrading easily via the screen, but you could theoretically use the root access to flash the image (I don't know how to do that though)

zevaryx, 2025-03-03:
And I'd appreciate it if you would not make fake guides

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

Tombraider2006, 2025-03-03:
> fake guides

what is the fake? if after my guides everything works) I perfectly understand those people who can make it work for them but can't explain it so that it works for others. I pointed out the problem with your guide. My guide works)

zevaryx, 2025-03-03:
Just translating what you posted in the telegram channel, since you posted an invite link. Again, just wanted full firmware transparency, since there is no firmware available for it directly from Creality as of yet besides messaging their support, and I want people to know exactly what changes were made. I'm a security engineer, so trying to keep things in the clear.

As for the problem with my guide and rolling back to stock not being listed, it's simply because I haven't dedicated the time to figure it out. I'll be keeping the root version in parity with whatever firmware comes out in the future, so there's be no missed features either way

Tombraider2006, 2025-03-03:
> Just translating what you posted in the telegram channel

translation error. Russian language is rich in idioms. the meaning is about the same but not so crude.

zevaryx, 2025-03-03:
Regardless, I added the build guide, and would be more than happy to test out a revert-to-stock method if you find one. For the meantime, I'm back to creating more fan shrouds to support BL-Touch and CR-Touch, as well as other leveling probes

zevaryx, 2025-03-03:
I will point out really quick, that the firmware you did link is in fact identical to the one I posted, so it's safe to use yours and I was never trying to say, "Hey, only use mine"

I just wanted people to know where the firmware came from to verify the changes on their own

Tombraider2006, 2025-03-03:
> never trying to say, "Hey, only use mine"

no problem. I indicated the authorship, made a link to your git, a little morning sarcasm in the telegram chat does not count)

zevaryx, 2025-03-03:
So, in theory, if you modify `/etc/ota_info` and change the `ota_version` to `1.0.0.0`, you should be able to install the stock v1.2.0.10 from my repo

zevaryx, 2025-03-03:
SSH as root then run

sed -i -e 's/6.2.0.10/1.0.0.0/g' /etc/ota_info

Download and put this on a flash drive

https://github.com/zevaryx/ender-5-max-firmware/raw/refs/heads/main/F004_ota_img_V1.2.0.10.img

Plug it into the printer and accept the update

This should work, but I'm unable to test

(I tried to join the Telegram and post this for the user requesting how to downgrade but I got kicked.... if you could share that would be great)

zevaryx, 2025-03-03:
The guide has also been posted in my repo

Tombraider2006, 2025-03-03:
> I tried to join the Telegram and post this for the user requesting how to downgrade but I got kicked

you need to pass the bot verification.

Closed 2025-03-03.

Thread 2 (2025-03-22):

Firmware won't update

Andrej8181, 2025-03-22:
Hi.
I'm trying to update rooted firmware to my max 5.
But when I insert usb to screen it recognise that usb is insert but it wont start to upload firmware.
I already try different usb sticks and sd cards.
Can you please help me?

Andrej8181, 2025-03-22:
But i have v1.2.0.15 firmware on printer.  I get it from creality.

Tombraider2006, 2025-03-22:
try ask  here https://github.com/zevaryx/ender-5-max-firmware
 This is the man who made the root

Tombraider2006, 2025-03-22:
> I get it from creality.

can you give link from creality there you get 1.2.0.15

Andrej8181, 2025-03-22:
Link isnt average anymore. I can send you firmware image. But later when I get home.

Tombraider2006, 2025-03-22:
> Link isnt average anymore. I can send you firmware image. But later when I get home.

link to goole disk will be great

Andrej8181, 2025-03-22:
Here it is: https://drive.google.com/file/d/1ZLdVSbyM0XFLBf14zyk3l17YmaJa7nY6/view?usp=sharing
It is almost nothing changed only few translations to english and filament change shuld be working...

Andrej8181, 2025-03-22:
Im still trying...I try a lot of diferent usb drives and sd cards and nothing...when I put it in screen usb it recognise usb but wont offer to upgrade firmware...so bad..

Tombraider2006, 2025-03-23:
> Im still trying...I try a lot of diferent usb drives and sd cards and nothing...when I put it in screen usb it recognise usb but wont offer to upgrade firmware...so bad..

https://github.com/zevaryx/ender-5-max-firmware/releases/latest

Andrej8181, 2025-03-23:
Unfortunately it is not working. I try both. Img

Tombraider2006, 2025-03-23:
> Unfortunately it is not working. I try both. Img

so and i...  try wait for zeveryx make something

Andrej8181, 2025-03-23:
Ok.
Did you update it to?

Andrej8181, 2025-03-23:
It is working now...thank you both for great work and help.

Closed 2025-03-23.

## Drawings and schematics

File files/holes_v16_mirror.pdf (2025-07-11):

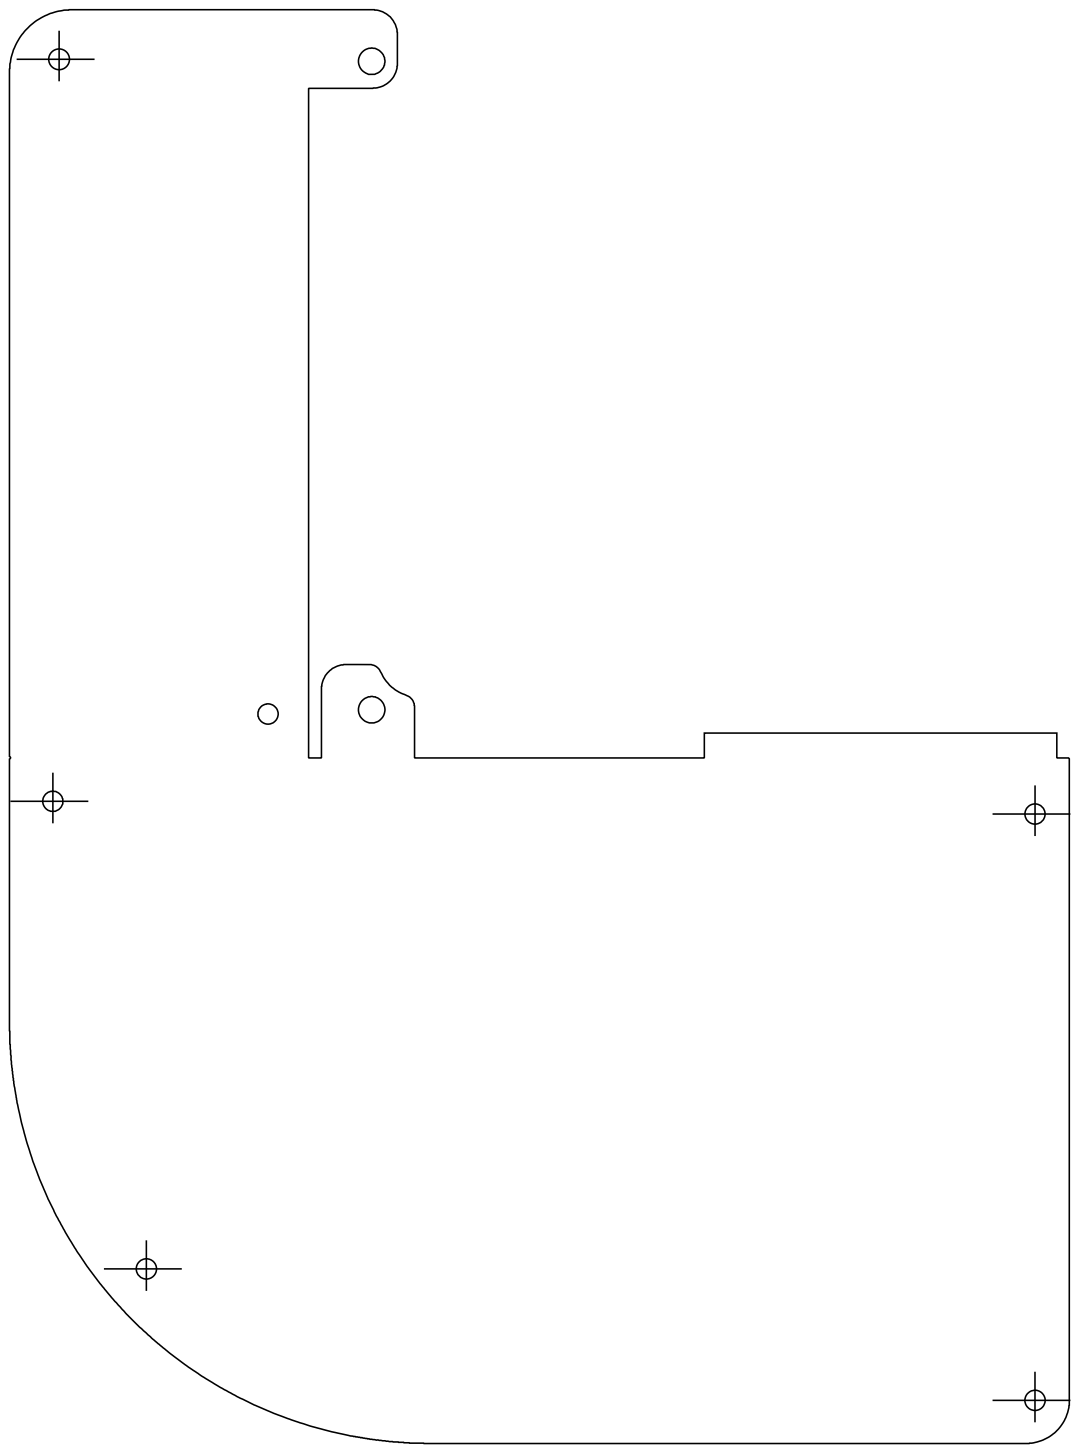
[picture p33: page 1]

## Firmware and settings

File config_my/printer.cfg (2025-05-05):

# CR-10 SE
# Printer_size: 400x400x400 #220x220x265
# Version: v1.2.10
# CreateDate: 2023/08/24
# Nozzle_mcu: chip: GD32F303CBT6
#             version: CR-NOZZLE_V21
# Leveling_mcu: chip: GD32E230F8P6
#             version: CR-K1-MAX-LEVELING-V1.0.0
# mcu: chip: GD32F303RET6
#      version: CR4NS200323C10
[include sensorless.cfg]
[include gcode_macro.cfg]
[include printer_params.cfg]
[include Helper-Script/save-zoffset.cfg]
[include Helper-Script/improved-shapers/improved-shapers.cfg]
[mcu]
serial:/dev/ttyS1
baud:230400
restart_method: command

[force_move]
enable_force_move: True
[mcu nozzle_mcu]
serial:/dev/ttyS7
baud: 230400
restart_method: command

[mcu leveling_mcu]
serial: /dev/ttyS6
baud: 230400
restart_method: command

[verify_heater extruder]
[verify_heater heater_bed]
check_gain_time: 120
heating_gain: 1.0
hysteresis: 10

[mcu rpi]
serial: /tmp/klipper_host_mcu

[bl24c16f]
i2c_mcu: rpi
i2c_bus: i2c.2
i2c_speed: 400000

[prtouch_v2]
z_offset: 0
step_base:2
pres_cnt: 4
show_msg: False
tilt_corr_dis: 0.00 #0.03
tri_min_hold: 8000 #12000 #4000 #1600
tri_max_hold: 16000 #26000 #8000 #6000
pres0_clk_pins: leveling_mcu:PA2
pres0_sdo_pins: leveling_mcu:PA0
pres1_clk_pins: leveling_mcu:PA5
pres1_sdo_pins: leveling_mcu:PA1
pres2_clk_pins: leveling_mcu:PA6
pres2_sdo_pins: leveling_mcu:PA3
pres3_clk_pins: leveling_mcu:PA7
pres3_sdo_pins: leveling_mcu:PA4
step_swap_pin: mcu:PA8 #PC10
pres_swap_pin: leveling_mcu:PB1 ##sync signal
speed: 3 #3#1.5
g28_wait_cool_down: true
noz_ex_com: 0.085 #0.082 #0.085 #0 #0.2
pa_clr_down_mm: -0.05
rdy_xy_spd: 300#100
clr_noz_start_x: -1 #130
clr_noz_start_y: 50 #390
clr_noz_len_x: 2  #60
clr_noz_len_y: 30 #45 #50 #2
pa_clr_dis_mm: 25 #35 #50
clr_xy_spd: 4
###quick clr nozzle
clr_noz_quick: True #False #True
clr_quick_high:0.7
clr_xy_quick_spd:100
clr_quick_times:10
clr_quick_react_dis:5

[hx711s]
count: 4
use_mcu: leveling_mcu
sensor0_clk_pin: leveling_mcu:PA2
sensor1_clk_pin: leveling_mcu:PA5
sensor2_clk_pin: leveling_mcu:PA6
sensor3_clk_pin: leveling_mcu:PA7
sensor0_sdo_pin: leveling_mcu:PA0
sensor1_sdo_pin: leveling_mcu:PA1
sensor2_sdo_pin: leveling_mcu:PA3
sensor3_sdo_pin: leveling_mcu:PA4


[printer]
kinematics: corexy#cartesian
max_velocity: 1000 #600
max_accel: 100000 #8000
max_accel_to_decel: 5000
max_z_velocity: 30
square_corner_velocity: 5.0
max_z_accel: 300

[idle_timeout]
timeout: 99999999

[stepper_x]
step_pin: PC2
dir_pin: !PB9
enable_pin: !PC3
microsteps: 32
rotation_distance: 63.874 #63.810 #63.95 #63.7 #64#40
endstop_pin: !PA11
#endstop_pin: tmc2209_stepper_x:virtual_endstop
#endstop_pin: nozzle_mcu: PB0
position_endstop: 400.5 #406 #400 #-30 #-10.5
position_min: -5 #-30 #-10.5
position_max: 406 #400 #400 #248
homing_speed: 40
homing_retract_dist:0 #10

[tmc2209 stepper_x]
uart_pin:PB12
driver_SGTHRS: 80#100#88
uart_address:3 
interpolate: True
run_current: 2.0 #1.2#0.65
sense_resistor: 0.150
stealthchop_threshold: 0
diag_pin: ^PB10

[stepper_y]
step_pin: PB8
dir_pin: PB7
enable_pin: !PC3
microsteps: 32
rotation_distance: 64.024 #63.912 #63.95 #63.7 #64 #60
endstop_pin: !PA12
#endstop_pin: tmc2209_stepper_y:virtual_endstop
position_endstop: 401 #400 #-15 #-5.5
position_min: -1 #-5 #-15 #-5.5
position_max: 401 #400 #225
homing_speed: 40
homing_retract_dist:0

[tmc2209 stepper_y]
uart_pin:PB13
driver_SGTHRS: 80
uart_address:3 
interpolate: True
run_current: 2.0 #1.2 #0.6
sense_resistor: 0.150
stealthchop_threshold: 0
diag_pin: ^PB11

[stepper_z]
step_pin: PB6
dir_pin: PB5#!PB5
enable_pin: !PC3
microsteps: 32
rotation_distance: 3.9930 #3.985 #4 #8
gear_ratio: 1:1 #64:20
endstop_pin: tmc2209_stepper_z:virtual_endstop#PA15   #probe:z_virtual_endstop
position_endstop: 0
position_max: 406.5 #405 #400 #270
position_min: -5 #-5

[tmc2209 stepper_z]
uart_pin: PB14
interpolate: True
run_current: 0.8
uart_address:3 
# hold_current:0.5
stealthchop_threshold: 0
sense_resistor: 0.150
diag_pin: PB0 #^PB14
# driver_SGTHRS: 0


[filament_switch_sensor filament_sensor]
switch_pin: !PC6
pause_on_runout: true
# runout_gcode: PAUSE

[output_pin _Height_module2]
pin: PA7
value: 1.0

[extruder]
max_extrude_only_distance:1000
max_extrude_cross_section:80
pressure_advance = 0.04
step_pin: nozzle_mcu: PB5
dir_pin: nozzle_mcu: PB4 #!nozzle_mcu: PB4
enable_pin: !nozzle_mcu: PB2
microsteps: 16
# gear_ratio: 42:12
rotation_distance: 6.72 #7.53
nozzle_diameter: 0.400
filament_diameter: 1.750
heater_pin: nozzle_mcu: PB8
sensor_type: EPCOS 100K B57560G104F
sensor_pin: nozzle_mcu: PA0
control = pid
pid_kp = 20.145
pid_ki = 1.919 
pid_kd = 52.881
min_temp: 0
max_temp: 320 # Set to 300 for S1 Pro


[tmc2209 extruder]
uart_pin: nozzle_mcu: PB10
# tx_pin: nozzle_mcu: PB11
run_current: 0.6 #0.7
sense_resistor: 0.15
stealthchop_threshold: 0
uart_address:3 


[accel_chip_proxy]
adxl345_cs_pin: nozzle_mcu:PA4
adxl345_spi_speed: 5000000
adxl345_axes_map: x,-z,y
adxl345_spi_software_sclk_pin: nozzle_mcu:PA5
adxl345_spi_software_mosi_pin: nozzle_mcu:PA7
adxl345_spi_software_miso_pin: nozzle_mcu:PA6

lis2dw_cs_pin: nozzle_mcu:PA4
lis2dw_spi_speed: 5000000
lis2dw_axes_map: x,-z,y
lis2dw_spi_software_sclk_pin: nozzle_mcu:PA5
lis2dw_spi_software_mosi_pin: nozzle_mcu:PA7
lis2dw_spi_software_miso_pin: nozzle_mcu:PA6

[resonance_tester]
accel_chip: accel_chip_proxy
accel_per_hz: 50
probe_points: 200,200,10


[heater_bed]
heater_pin: PA4 #PB2
sensor_type: EPCOS 100K B57560G104F
sensor_pin: PC4
#control = watermark
control = pid
pid_kp = 30    #37
pid_ki = 0.075 #0.10
pid_kd = 800   #1000
min_temp: -30
max_temp: 130
#temp_offset_flag = True

[temperature_sensor mcu_temp]
sensor_type: temperature_mcu
min_temp: 0
max_temp: 100


#############FAN OLD CONFIG
[controller_fan MCU_fan] # включаем обдув после включения драйверов
pin: PB1
max_power: 1.0
fan_speed: 1
kick_start_time: 0
stepper: stepper_x



[heater_fan nozzle_fan]
pin: !nozzle_mcu: PB3
max_power: 1.0
shutdown_speed: 0
cycle_time: 0.1
hardware_pwm: False
kick_start_time: 0.100
off_below: 0.0
heater: extruder
fan_speed: 1.0
heater_temp: 60.0
[output_pin en_nozzle_fan]
pin: nozzle_mcu: PB7
pwm: False
value: 1.0

###喷头前面风扇
[output_pin fan0]
pin: !nozzle_mcu:PB15
pwm: True
cycle_time: 0.01
hardware_pwm: false
value: 0.00
scale: 255
shutdown_value: 0.0
[output_pin en_fan0]
pin: nozzle_mcu: PB6
pwm: False
value: 1.0

###喷头后面风扇
[output_pin fan1]
pin: !nozzle_mcu:PA9
pwm: True
cycle_time: 0.01
hardware_pwm: false
value: 0.00
scale: 255
shutdown_value: 0.0
[output_pin en_fan1]
pin: nozzle_mcu: PB9
pwm: False
value: 1.0




###led
[output_pin green_pin]
pin: PA0
value: 0.0
[output_pin red_pin]
pin: PC1
value: 0.0
[output_pin yellow_pin]
pin: PA1
value: 1.0
[output_pin light_pin]
#pin: nozzle_mcu: PB0 #PA10
pin: !PC0
value: 0.0


[filter]
hft_hz: 1
lft_k1: 0.95
lft_k1_oft: 0.95
lft_k1_cal: 0.95

[dirzctl]
use_mcu: mcu
step_base: 2


[bed_mesh]
speed: 350 #350
mesh_min: 5,5        #need to handle head distance with bl_touch
mesh_max: 395,395 #215,215       #max probe range
probe_count: 8,8 #6,6 #7,7
fade_start: 3.0#1
fade_end: 10
fade_target: 0
mesh_pps:2,2
algorithm: bicubic
bicubic_tension: 1

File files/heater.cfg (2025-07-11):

[mcu expander]
serial: /dev/serial/by-id/usb-Klipper_stm32f042x6_120031001653304B4D323431-if00
restart_method: command
#========================================================
#=================== iHeaterS cfg (Beta 1) ==============
#========================================================

# Изменения 2025-05-21_23-15-34:
# - Добавлены заголовки секций с описанием их назначения.
# - Код отформатирован для удобочитаемости: добавлены отступы, пустые строки, выровнены параметры.
# - Добавлены комментарии на русском к каждой строке кода, включая G-код внутри макросов.
# - Код помечен как Beta 1.

### Секция 1: Определение пинов iHeaterS
# Описание: Эта секция описывает пины, используемые для подключения нагревателя, датчиков температуры и вентиляторов. Секция закомментирована, так как используется [duplicate_pin_override] из другого файла конфигурации (например, printer.cfg).
#===================== iHeaterS pins =====================
# Разрешение повторного использования пинов для гибкости подключения
[duplicate_pin_override]              # Определяет возможность повторного использования пинов (закомментировано)
pins:                                 # Список пинов для повторного использования (закомментировано)
    expander:PA5,                             # Пин PC0: используется для управления нагревателем Heater_TT
    expander:PA6,
    expander:PA3                     # Пин PC5: используется для датчика температуры (совместно с chamber_temp)
#    PB1,                             # Пин PB1: используется для управления вентилятором chamber_heater_fan
#    PC8                              # Пин PC8: используется для управления выдувным вентилятором blower_fan
# Пины для нагревателя, датчиков и вентиляторов (PC5 используется для двух датчиков)

### Секция 2: Конфигурация iHeaterS
# Описание: Настройка оборудования для управления нагревателем камеры (Heater_TT), вентиляторами (chamber_heater_fan, blower_fan) и датчиком температуры (Heater_TS). Включает параметры PID-регулирования и проверки нагрева.
#==================== iHeaterS CONFIG ====================
# Рекомендация по калибровке PID для нагревателя камеры:
#🔥🔥🔥🔥🔥🔥🔥🔥🔥🔥🔥🔥🔥🔥🔥🔥🔥🔥🔥🔥🔥🔥🔥🔥🔥🔥🔥🔥
#     PID_CALIBRATE HEATER=Heater_TT TARGET=45         # Команда для калибровки PID на температуре 45°C
#     PID parameters for 45°C:                         # Параметры PID для температуры 45°C:
#                            pid_Kp=65.373             # Коэффициент пропорциональности (Kp) для PID
#                            pid_Ki=0.214              # Коэффициент интегральности (Ki) для PID
#                            pid_Kd=4993.676           # Коэффициент дифференциальности (Kd) для PID
#🔥🔥🔥🔥🔥🔥🔥🔥🔥🔥🔥🔥🔥🔥🔥🔥🔥🔥🔥🔥🔥🔥🔥🔥🔥🔥🔥🔥
# Это необходимо для точного и стабильного нагрева камеры.
# Без калибровки PID температура может превышать заданную или стабилизироваться слишком медленно!

[heater_generic Heater_TT]                # Определение нагревателя Heater_TT для камеры
heater_pin: expander:PA0                  # Пин для управления нагревателем 
max_power: 0.7                            # Максимальная мощность нагревателя (90% от возможной)
sensor_type: EPCOS 100K B57560G104F       # Тип датчика температуры (термистор EPCOS 100K)
sensor_pin: expander:PA6                  # Пин для подключения датчика температуры (PC5)
pwm_cycle_time: 0.3                       # Время цикла ШИМ для управления нагревателем (0.3 секунды)
min_temp: 0                               # Минимальная допустимая температура (°C)
max_temp: 120                             # Максимальная допустимая температура (°C)
control: pid                              # Метод управления нагревателем (PID-регулирование)
pid_Kp: 65.373                            # Коэффициент пропорциональности PID (Kp)
pid_Ki: 0.214                             # Коэффициент интегральности PID (Ki)
pid_Kd: 4993.676                          # Коэффициент дифференциальности PID (Kd)

[verify_heater Heater_TT]                 # Проверка работы нагревателя Heater_TT
max_error: 240                            # Максимально допустимая ошибка температуры (градусов)
check_gain_time: 1800                     # Время проверки набора температуры (секунд)
heating_gain: 1                           # Минимальный прирост температуры для проверки (°C)


#[chamber_fan chamber_fan]
#pin: expander:PA0 
#max_power: 0.7
#shutdown_speed: 0
#kick_start_time: 0.5
#heater: Heater_TT
#fan_speed: 1.0
#off_below: 0
#idle_timeout:30
#idle_speed:0.5

[heater_fan chamber_heater_fan]           # Вентилятор, связанный с нагревателем камеры (chamber_heater_fan)
pin: expander:PA1                         # Пин для управления вентилятором (PB1)
heater: Heater_TT                         # Нагреватель, с которым связан вентилятор (Heater_TT)
heater_temp: 35.0                         # Температура нагревателя, при которой вентилятор включается (°C)
fan_speed: 1.0                            # Скорость вентилятора при включении (1.0 = 100%)
shutdown_speed: 0                         # Скорость вентилятора при выключении принтера (0 = выключен)
kick_start_time: 0.5                      # Время начального импульса для старта вентилятора (секунд)

[temperature_sensor Heater_TS]            # Датчик температуры камеры (Heater_TS)
sensor_pin: expander:PA6                  # Пин для подключения датчика температуры (PC5)
sensor_type: Generic 3950                 # Тип датчика температуры (термистор EPCOS 100K)
min_temp: 0                               # Минимальная допустимая температура (°C)
max_temp: 140                             # Максимальная допустимая температура (°C)
[temperature_sensor Heater_TW]            # Датчик температуры камеры (Heater_TS)
sensor_pin: expander:PA5                  # Пин для подключения датчика температуры (PC5)
sensor_type: Generic 3950                 # Тип датчика температуры (термистор EPCOS 100K)
min_temp: 0                               # Минимальная допустимая температура (°C)
max_temp: 140  
[temperature_fan blower_fan]              # Вентилятор для охлаждения камеры (blower_fan), управляемый температурой
pin: expander:PA3                         # Пин для управления вентилятором (PC8)
cycle_time: 0.0100                        # Время цикла ШИМ для управления вентилятором (0.01 секунды)
hardware_pwm: false                       # Использование аппаратного ШИМ (отключено)
max_power: 0.6                             # Максимальная мощность вентилятора (1.0 = 100%)
shutdown_speed: 0                         # Скорость вентилятора при выключении принтера (0 = выключен)
sensor_type: EPCOS 100K B57560G104F       # Тип датчика температуры (термистор EPCOS 100K)
sensor_pin: expander:PA6                  # Пин для подключения датчика температуры (PC5)
min_temp: 0                               # Минимальная допустимая температура (°C)
max_temp: 70                              # Максимальная допустимая температура (°C)
control: watermark                        # Метод управления вентилятором (watermark — по порогу температуры)
max_delta: 0.5                            # Максимальная разница температур для управления (°C)
max_speed: 1.0                            # Максимальная скорость вентилятора (1.0 = 100%)
min_speed: 0.0 

[fan_generic back_fans]
pin: expander:PA3                         # Пин для управления вентилятором (PC8)
cycle_time: 0.0100                        # Время цикла ШИМ для управления вентилятором (0.01 секунды)
hardware_pwm: false                       # Использование аппаратного ШИМ (отключено)
max_power: 1                              # Максимальная мощность вентилятора (1.0 = 100%)
shutdown_speed: 0                         # Скорость вентилятора при выключении принтера (0 = выключен)
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

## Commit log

2025-02-19 артикли
2025-03-21 правки конфига
    [gcode_macro.cfg, printer.cfg, sensorless.cfg]
2025-03-22 пояснения
2025-03-23 ссылку поправил
2025-03-25 правки вентилятор
    [gcode_macro.cfg, printer.cfg]
2025-03-25 правки
2025-04-01 sfs правки дополнения
2025-04-22 струтурировал
2025-05-05 1.2.0.20 обновление
2025-05-05 светлый путь
2025-05-05 добавил информацию о прошивке
2025-05-11 замена хотенда
2025-05-21 обновление
2025-07-01 stl add
    [heater_v16.stl]
2025-07-25 петли кастомные
2025-07-25 кастомные петли
2025-09-18 автоматический скрпит
2025-09-18 убрал проверку сертификата
2025-09-18 исправлено
2025-09-18 правки перезапуска клиппера
2025-09-18 промежуточная версия
2025-09-18 вроде
2025-09-18 еще чуть чуть
2025-09-18 77 версия
2025-09-18 ну уже
2025-09-18 100 процентов
